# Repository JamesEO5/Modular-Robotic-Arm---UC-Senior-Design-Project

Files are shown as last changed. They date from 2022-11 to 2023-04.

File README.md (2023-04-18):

# Modular-Robotic-Arm---UC-Senior-Design-Project
This is a Modular Robot arm designed to be simple to build and modify. The target audience is grade school and high school students interested in STEM. All files needed to build this robot can be accessed in this database. An instruction manual is also added so that anyone interested in constructing this robot is able to in the easiest way possible. 

To navigate this site click on the desired folder to view each file and download them. 
The instruction manual should be your first resource since it contains links to all of the stp files needed for the build as well as links to all of the purchaseable parts needed. 

This github page was created by James O'Meara with the help from Charles Watson and Roger Farnham.

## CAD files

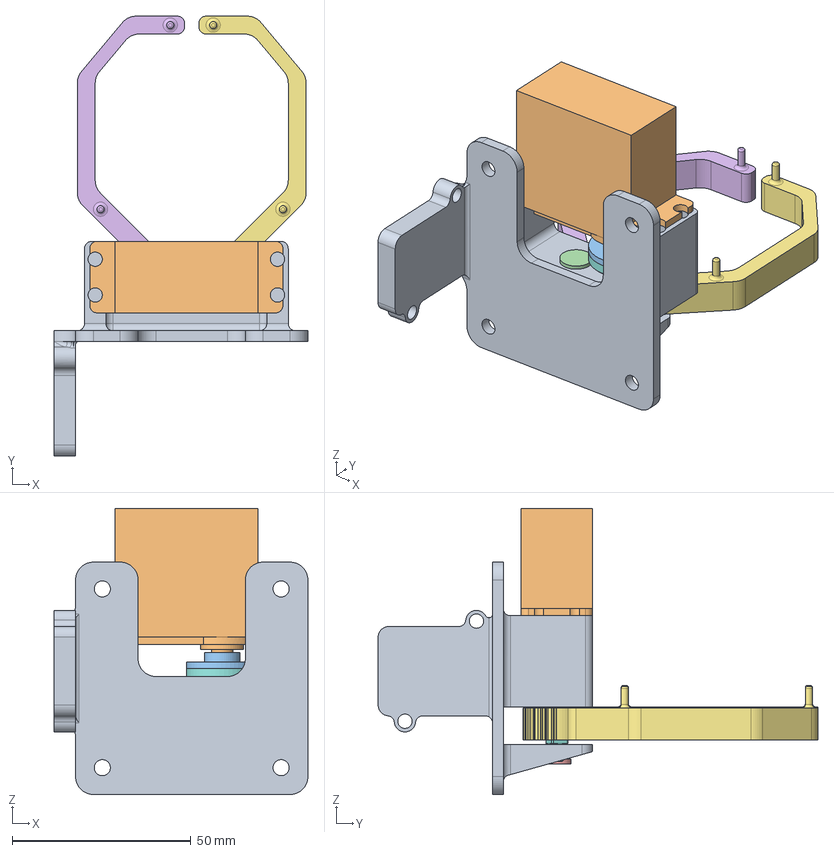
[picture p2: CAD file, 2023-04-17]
3D Files/Claw/ClawAssembly.stp
71.0 x 123.0 x 80.0 mm
ClawBody
MG996R_10KGSERVO
FlangeHorn
claw shaft
ClawShaftSpacer
Gripper_Left
Gripper_Right
Driveshaft_Claw

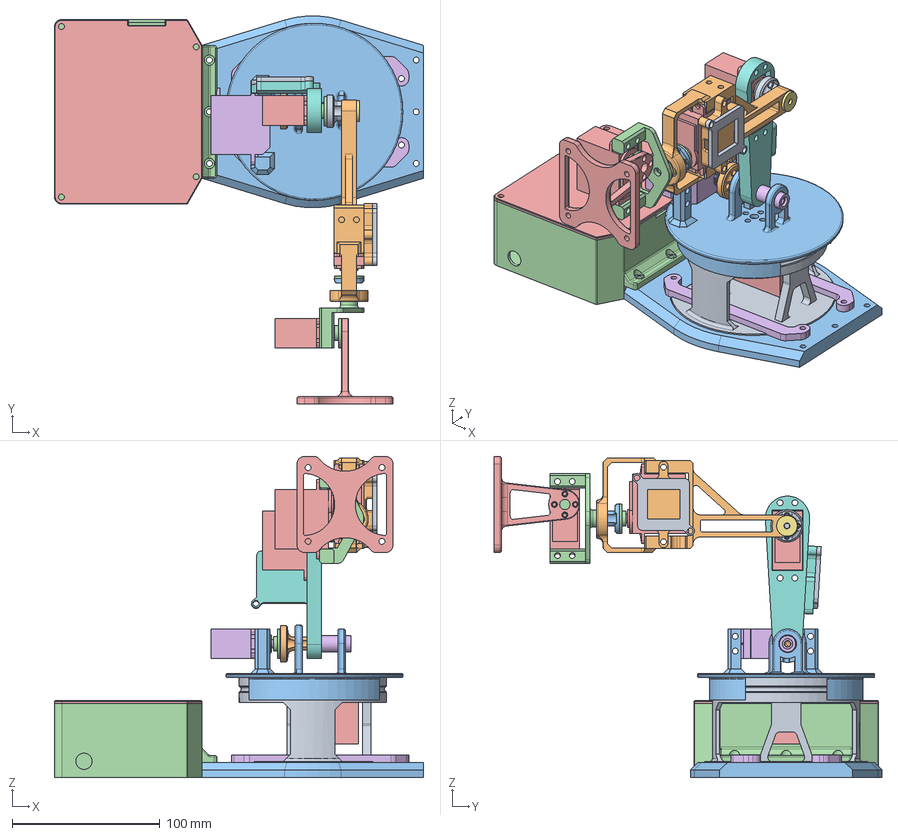
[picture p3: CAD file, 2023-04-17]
3D Files/Arm/MainAssembly.stp
250.0 x 262.8 x 217.4 mm
Base
DriveshaftLower
Turntable
FlangeHorn x 5
MG996R_10KGSERVO x 4
DS3225MG_25KGSERVO
10x15bearing x 2
Link1
DriveshaftUpper
Link2
BearingShaftA
BearingPlate
EEPlate
SupportBushing
UpperLinkWasher
JB_Link1
JB_Lid x 2
JB_Link2
BP_Center
BP_EBox
BP_EBox_Lid
HoldingBar x 2

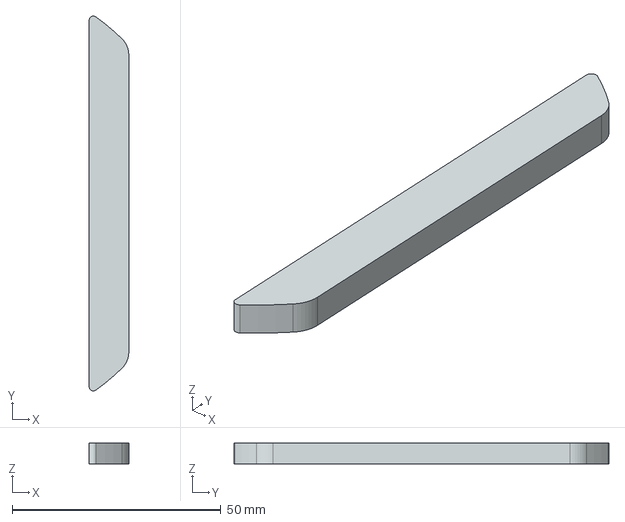
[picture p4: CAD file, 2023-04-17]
3D Files/Arm/BP_Spacer.stp
9.50 x 89.7 x 5.00 mm

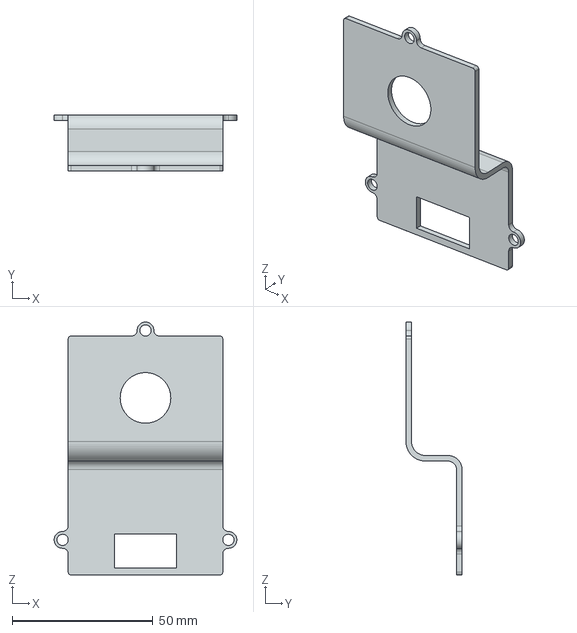
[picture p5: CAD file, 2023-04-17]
3D Files/Camera Holder/CM_Lid.stp
65.0 x 20.0 x 90.0 mm

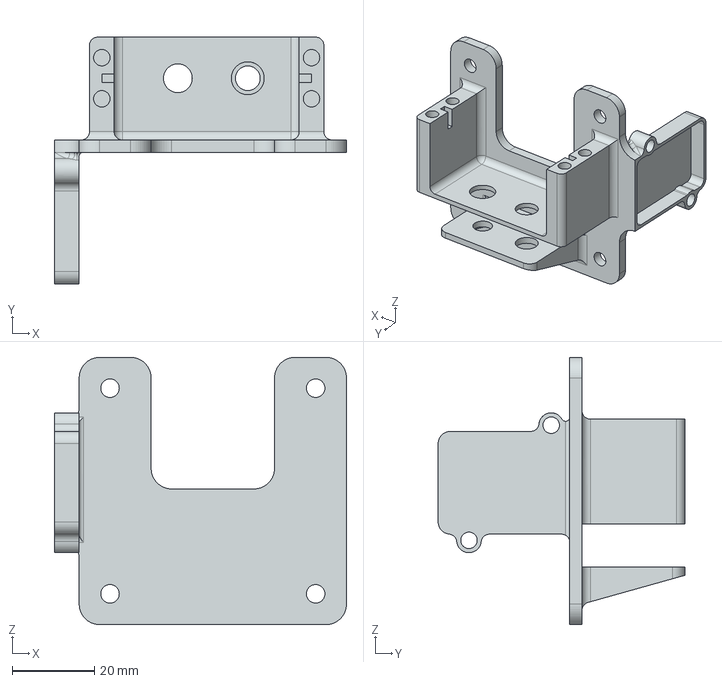
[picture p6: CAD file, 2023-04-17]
3D Files/Claw/ClawBody.stp
71.0 x 60.0 x 65.0 mm

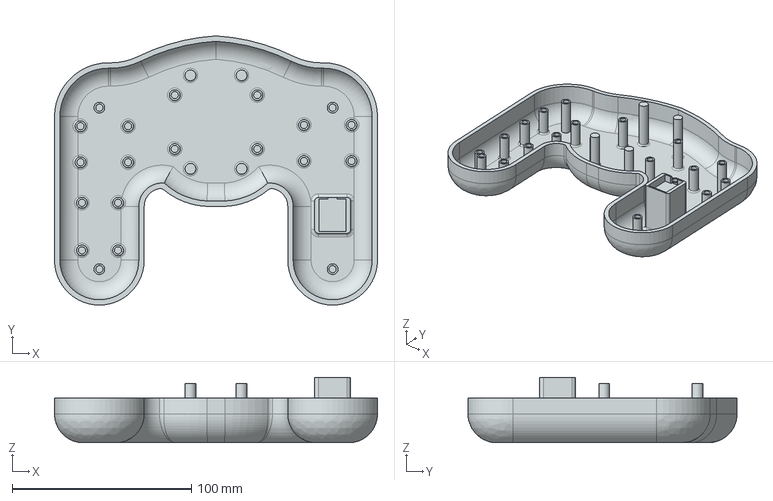
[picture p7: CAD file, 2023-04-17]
3D Files/Controller/Controller Bottom v2.stp
180.0 x 150.0 x 36.5 mm

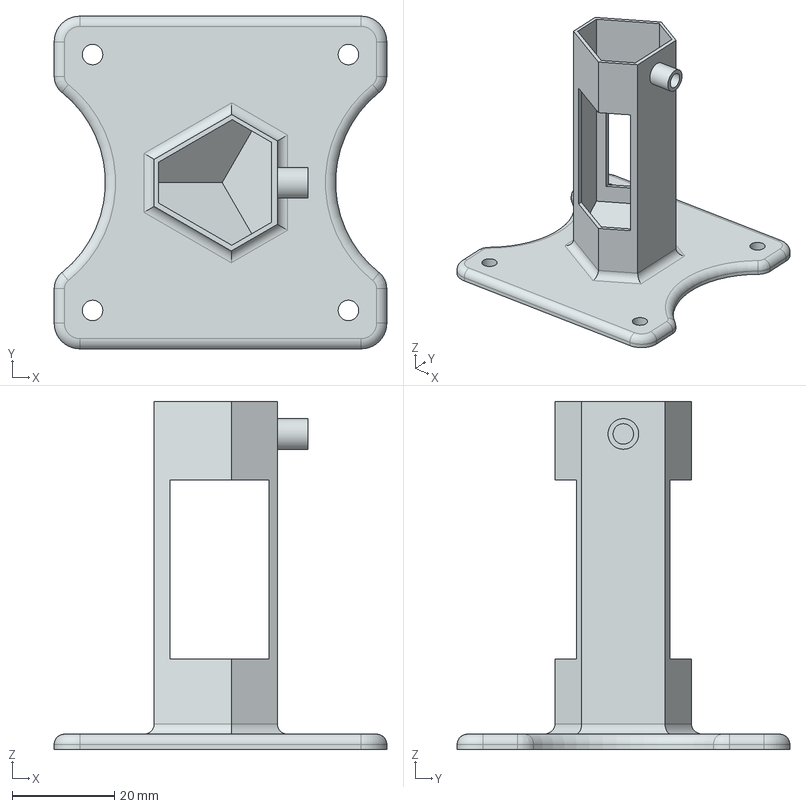
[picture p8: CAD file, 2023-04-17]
3D Files/Pen Holder/Pen end effector V6.stp
65.0 x 65.0 x 68.0 mm

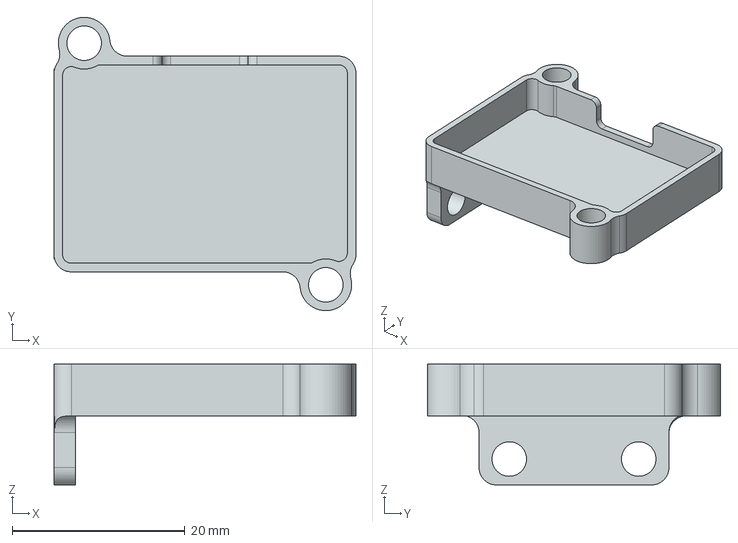
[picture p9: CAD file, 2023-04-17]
3D Files/Arm/JB_EEPlate.stp
35.0 x 34.0 x 14.0 mm

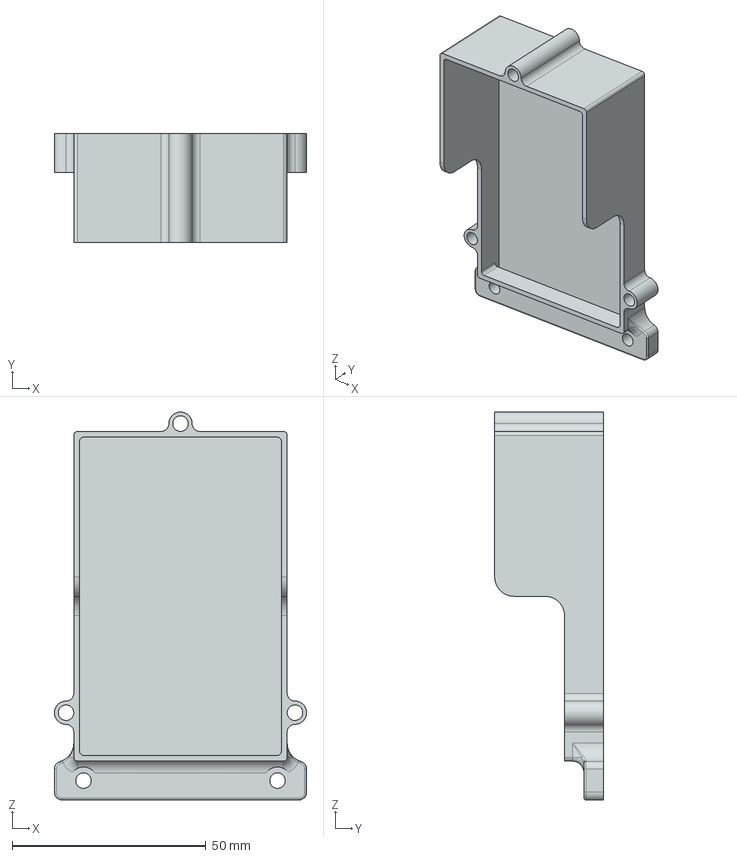
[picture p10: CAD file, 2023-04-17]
3D Files/Camera Holder/CM_Body.stp
65.0 x 28.0 x 100.0 mm

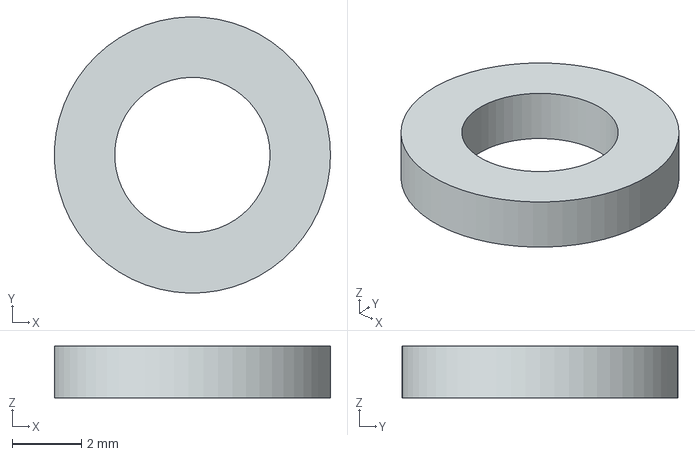
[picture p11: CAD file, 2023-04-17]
3D Files/Claw/ClawShaftSpacer.stp
7.99 x 8.00 x 1.50 mm

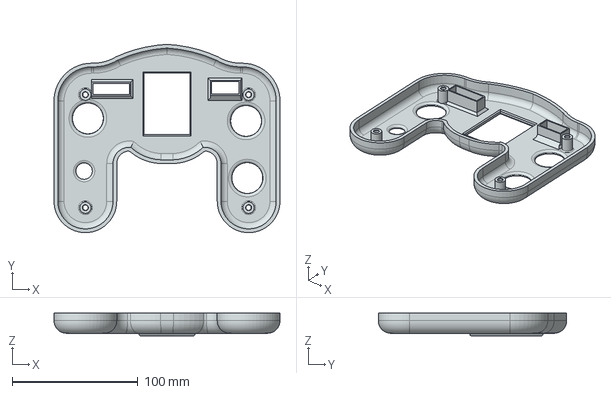
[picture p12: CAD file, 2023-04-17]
3D Files/Controller/Controller top v4.stp
180.0 x 150.0 x 18.0 mm

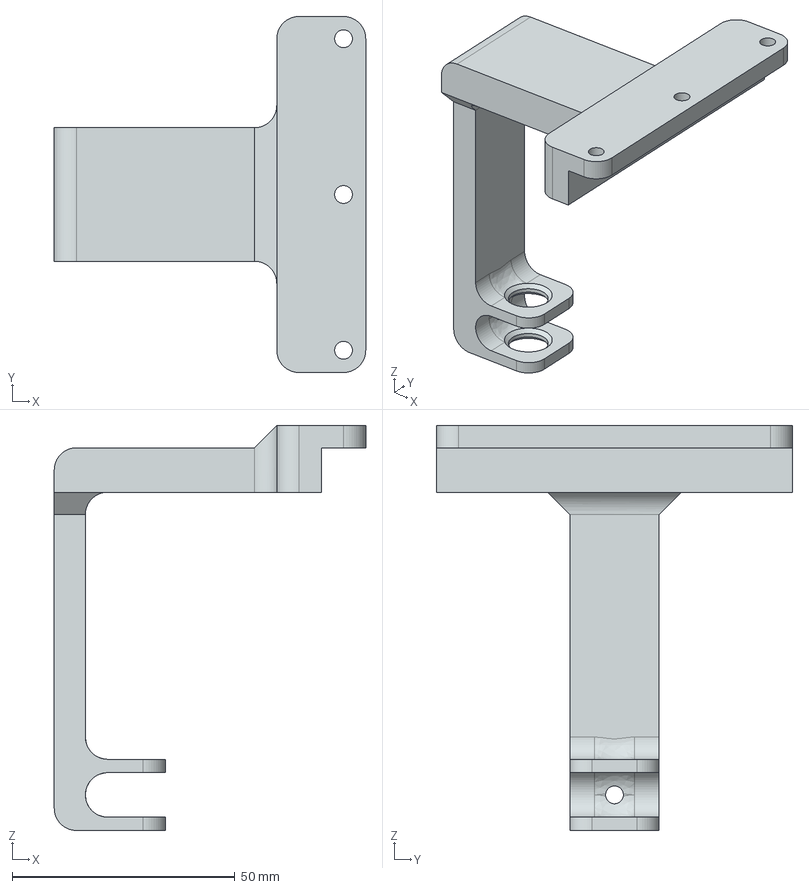
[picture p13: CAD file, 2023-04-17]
3D Files/Arm/BP_ClampPlate.stp
70.0 x 80.0 x 91.0 mm

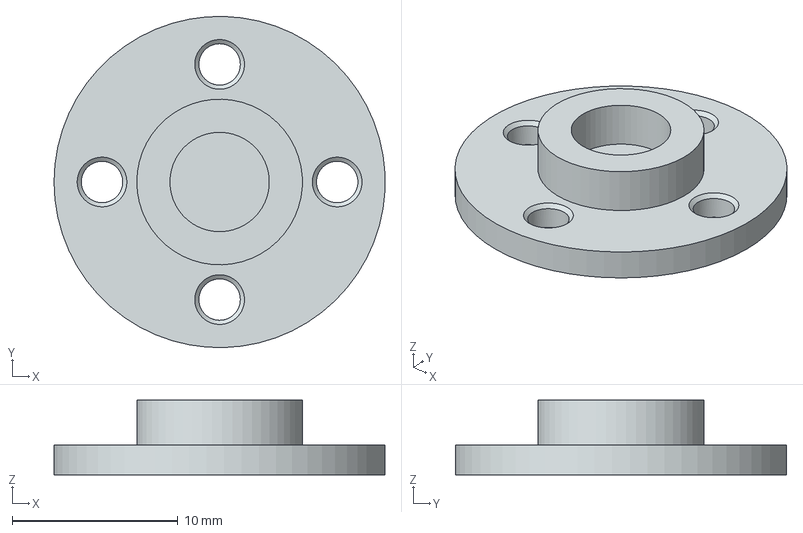
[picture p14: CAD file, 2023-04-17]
3D Files/Claw/FlangeHorn.stp
20.0 x 20.0 x 4.50 mm

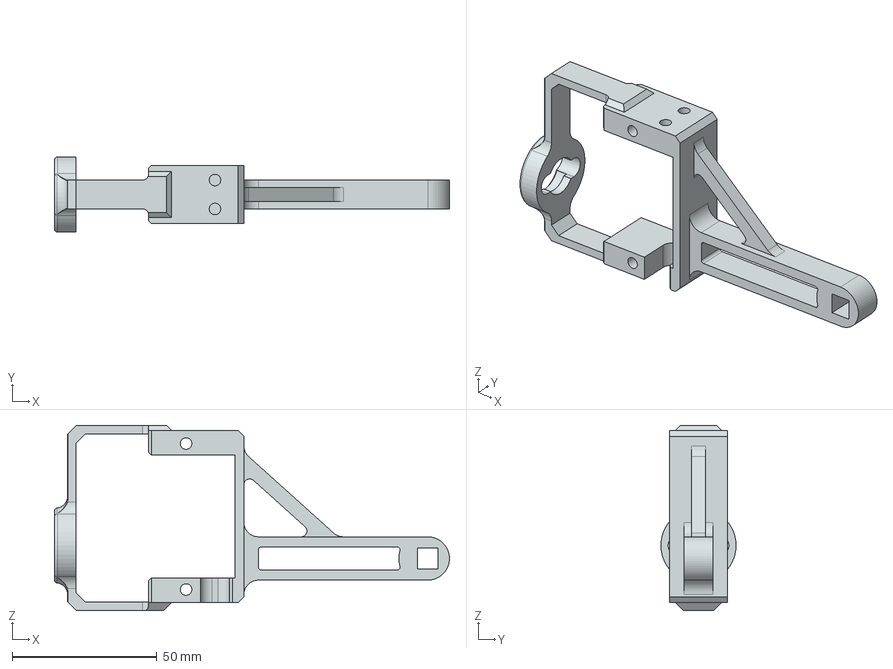
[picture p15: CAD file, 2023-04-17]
3D Files/Arm/Link2.stp
136.6 x 26.0 x 64.0 mm

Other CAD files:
3D Files/Arm/DriveshaftUpper.stp
3D Files/Claw/Gripper_Right.stp
3D Files/Arm/BearingPlate.stp
3D Files/Claw/claw shaft.stp
3D Files/Arm/10x15bearing.stp
3D Files/Arm/BP_Center.stp
3D Files/Arm/BP_ClampFoot.stp
3D Files/Arm/BP_ClampScrew.stp
3D Files/Arm/BP_ClampShaft.stp
3D Files/Arm/BP_EBox.stp
3D Files/Arm/BP_EBox_Lid.stp
3D Files/Arm/Base.stp
3D Files/Arm/BearingRetainer.stp
3D Files/Arm/BearingShaftA.stp
3D Files/Arm/ClawBody.stp
3D Files/Arm/DriveshaftLower.stp
3D Files/Arm/EEPlate.stp
3D Files/Arm/FlangeHorn.stp
3D Files/Arm/HoldingBar.stp
3D Files/Arm/JB_Lid.stp
3D Files/Arm/JB_Lid_EEPlate.stp
3D Files/Arm/JB_Link1.stp
3D Files/Arm/JB_Link2.stp
3D Files/Arm/Link1.stp
3D Files/Arm/SupportBushing.stp
3D Files/Arm/Turntable.stp
3D Files/Arm/UpperLinkWasher.stp
3D Files/Arm/servo.stp
3D Files/Claw/Driveshaft_Claw.stp
3D Files/Claw/Gripper_Left.stp

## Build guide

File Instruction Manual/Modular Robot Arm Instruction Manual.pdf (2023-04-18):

## USER MANUAL

# Modular Robotic Arm

### 3D Printed Modular Robot Arm

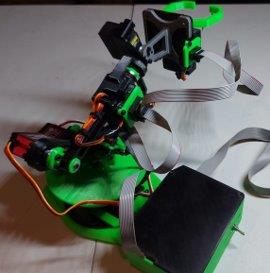
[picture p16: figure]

This document explains how to construct, use, and troubleshoot a 3D printed Modular Robot Arm. This robot arm uses a Arduino board to register inputs made by the user on a controller and use those inputs to control the servos on the arm. The modular design of this robot also encourages users to create their own features. All components of this arm are openly available online so that anyone can gather the materials themselves and build it. The open source code is also available so a user can modify to match their needs.

Note Read through the entire manual before assembling the robot. This will ensure no important information is missed before assembly.

# Contents

2 | Modular Robot Arm Manual

# Open Source Resources

All Files can be found on the git hub page.
- Git hub files are found at this link. (https://github.com/JamesEO5/Modular-Robotic-Arm---UC-Senior-Design-Project)
- If this is not a pdf document then they can be found at:
- https://github.com/JamesEO5/Modular-Robotic-Arm---UC-Senior-Design-Project

# Tools Required

1. #25 Allen Key
2. #25 Phillips Head Screwdriver
3. Soldering Iron
4. Pliers jjbjbjb

jij

# Safety Guidelines

Caution Observe all instructions and cautions in the user documentation. Constructing the robot
arm in a manner not specified can damage the robot arm and injure the user.

Caution The protection provided by the model can be impaired if it is used in a manner not described in the user documentation.

Caution Electrical shock hazard. This device contains electrical components and capacitors. Do
not disassemble the electronics ofhe robot while it is in operation and be sure to discharge the capacitors before disassembly.

Caution Risk of fire if electrical shorts occur. Some 3D printed plastics can burn and catch on fire.

# EMC Notices

Refer to the following notices for prevention measures necessary to ensure the specified EMC performance.

Notice For EMC declarations and certifications, and additional information, refer to the Product Certifications and Declarations section.

Notice The performance of this product can be disrupted if subjected to Electrostatic Discharge (ESD) during operation. To prevent damage, industry- standard ESD prevention measures must be employed during installation, maintenance, and operation.

# Purchasable Parts

## Mechanical Components

1. #25 Screws
2. Servo Horns
3. M3 x 5mm Female Press In Inserts

## Cables

1. 8 Pin Ribbon Connectors
2. 20 Pin Ribbon Connectors
3. 8 Pin Ribbon Cable
4. 20 Pin Ribbon Cable

## Electrical Components

1. Power Adapter
2. Power Supply
3. 25kg Servo
4. 10kg Servo

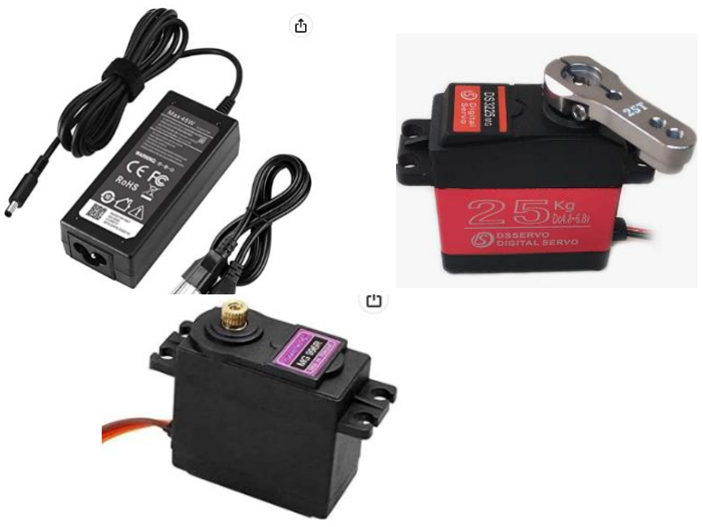
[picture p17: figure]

# 3D Printed Parts

## Base

1. Base
2. BP_Center
3. BP_EBox
4. BP_EBox_Lid
5. HoldingBar
6. Turntable
7. ClampFoot
8. ClampSHaft
9. ClampPlate
10.BearingShaftA
11.DriveshaftLower

## Link 1

1. Link1
2. JB_EEPlate
3. JB_Link1

## Link 2

1. Link 2
2. BearingPlate
3. JB_Lid_EEPlate
4. EEPlate
5. JB_Lid
6. JB_Link2
7. DriveshaftUpper
8. UpperLinkWasher

## Gripper

1. ClawBody
2. Gripper_Right
3. Gripper_Left
4. Driveshaft_Claw
5. Claw_Shaft
6. ClawShaftSpacer

## Controller

1. Controller_Top
2. Controller_Bottom

# Before Assembly

Complete the following tasks before building the Modular Robot Arm. It is very important that you complete the tasks before building to ensure easy assembly and best performance.
1. Purchase all necessary parts.
2. Print all parts that need to be 3D printed.
3. Be sure your work surface is completely free of other materials not related to the build.

# Wiring Instructions

## Controller

1 | Start by soldering the 8 and 20 pin connector to the controller motherboard. Then solder the straight 8 pin connector to the bottom section of the controller board
2 | Flip the board over and solder 5 wires to the underside of the board according to the picture seen Then connect the J3 joystick to the wires as seen
3 | Turn the board back over to the top side and solder 5 wires to the top of the board Then solder those wires to the J1 joystick as seen

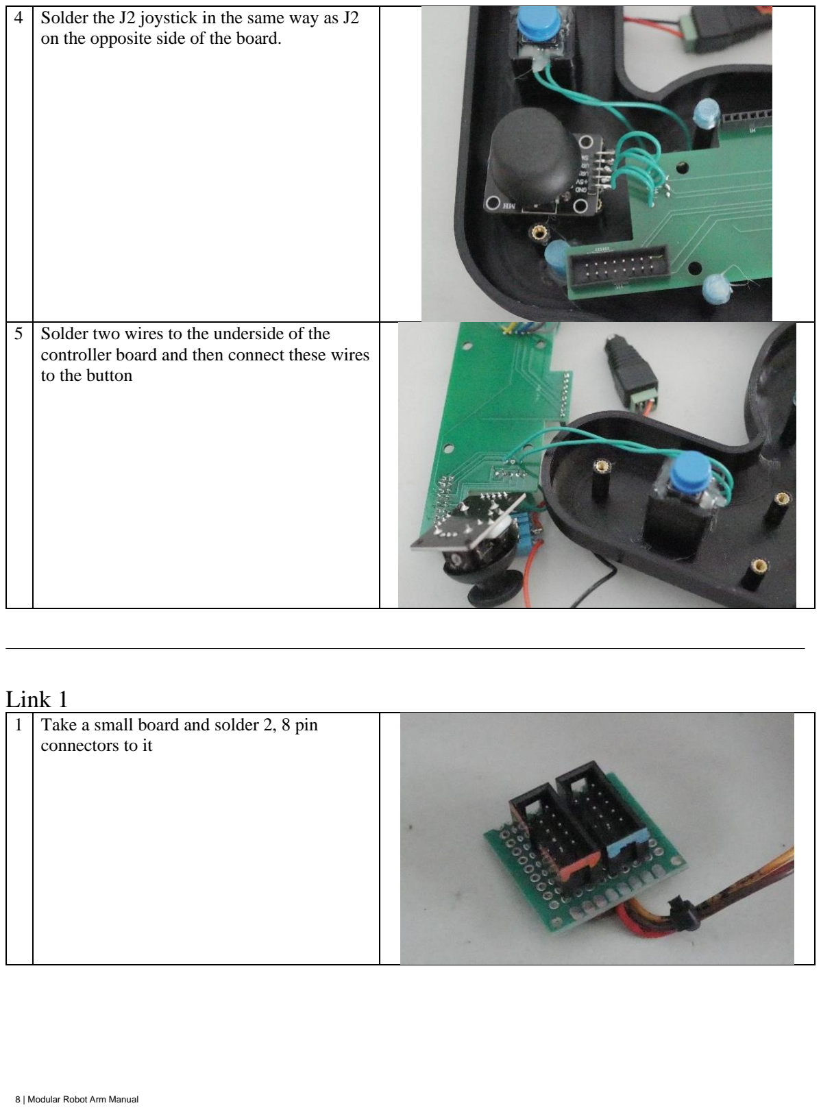
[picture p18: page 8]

4 | Solder the J2 joystick in the same way as J2 on the opposite side of the board.
5 | Solder two wires to the underside of the controller board and then connect these wires to the button

## Link 1

1 Take a small board and solder 2, 8 pin connectors to it

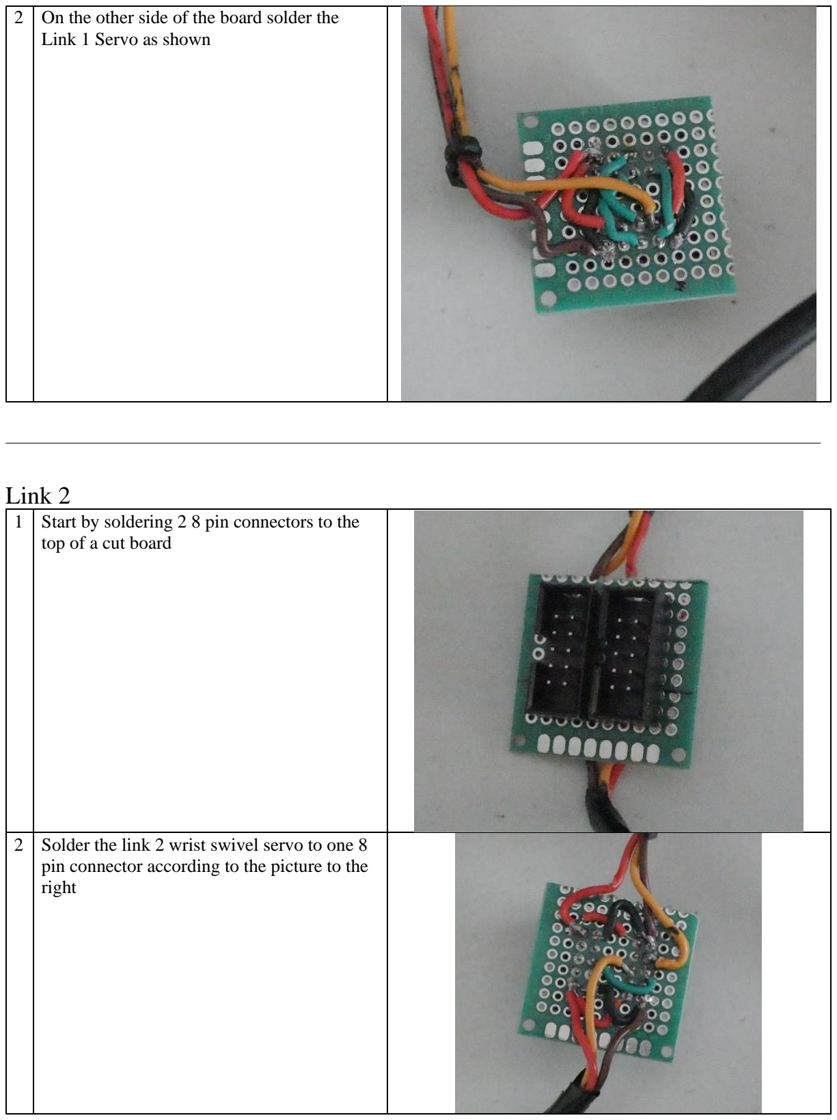
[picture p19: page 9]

2 On the other side of the board solder the Link 1 Servo as shown

## Link 2

1 | Start by soldering 2 8 pin connectors to the top of a cut board
2 | Solder the link 2 wrist swivel servo to one 8 pin connector according to the picture to the right

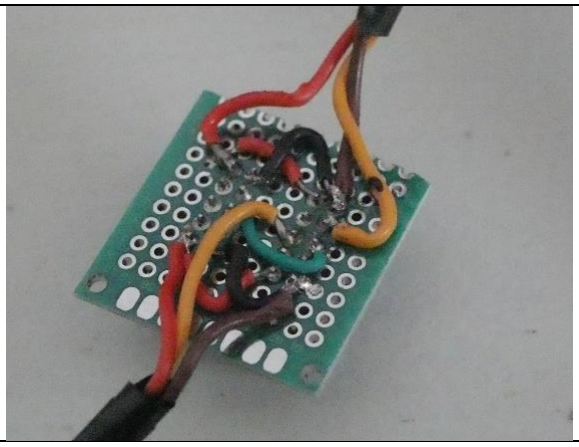
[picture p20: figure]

3 Solder the link 2 wrist bend servo to the other 8 pin connector according to the picture to the right

## Gripper

1 | Solder the 8 pin connector to a small board
2 | Solder the gripper servo to the board as seen on the right

## Main Board

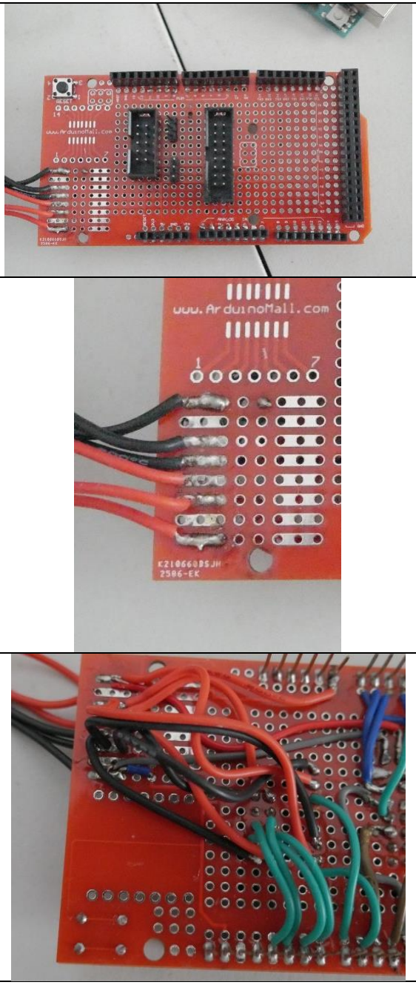
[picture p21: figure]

1 | Solder an 8 pin connector, a 20 pin connector, and 2 3 pin connectors to a Arduino cover board as shown
2 | Solder 3 black wires and 3 red wires to the side of the board as shown
3 | Flip the board over and solder red and black wires to the board as shown to the right

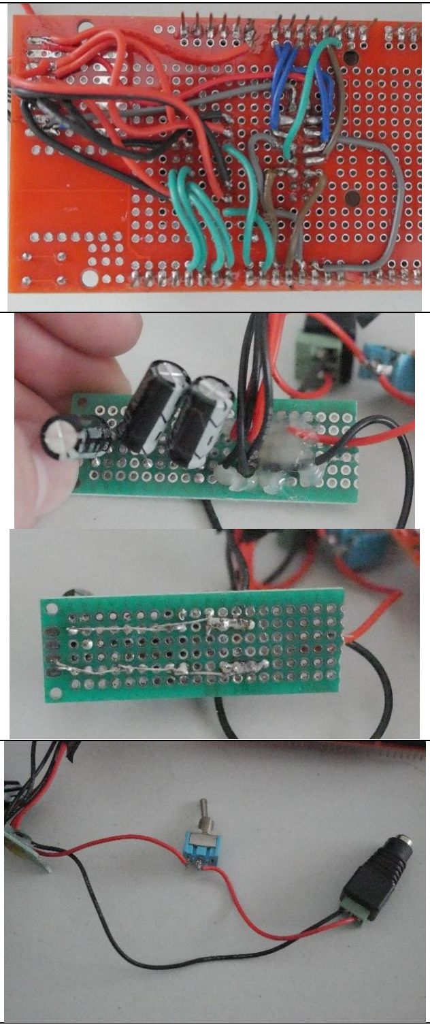
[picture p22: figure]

4 | Solder the rest of the blue and green wires to the board as shown to the right. These wires are for the pin outs for the servos and controller
5 | Take another small board and solder the red and black wires coming off the board in parallel with their respective colors. Then solder 3 capacitors in parallel with the red and black wires
6 | Finally solder a power input in series with the red and black wires and add a switch to the red wire. Wire it according to the picture to the right

# Build Instructions

When building the robot arm use the #25 screw driver on all Phillips head screws and a #25 allen wrench on all other fasteners. Follow the instructions carefully and follow each step to ensure no components are damaged during the build process. Be sure to also follow all wiring guides mentioned so no wires get entangled during operation.

## Gripper

1 | Parts Required: 1. 10 short screws 2. 2 medium screws 3. 1 servo bracket screw 4. gripper pin 5. Washer 6. Aluminum servo interface bracket 7. Gripper interface pin 8. Servo circuit board cover 9. Left and right grippers 10. 10 kg Servo 11. Servo Bracket 12. Hand Connector bracket
2 | Place the Hand connector bracket on the large flat surface of the servo bracket and secure it with 4 short screws
3 | Snap on the aluminum servo interface bracket onto the 10kg servo and secure it with the servo screw

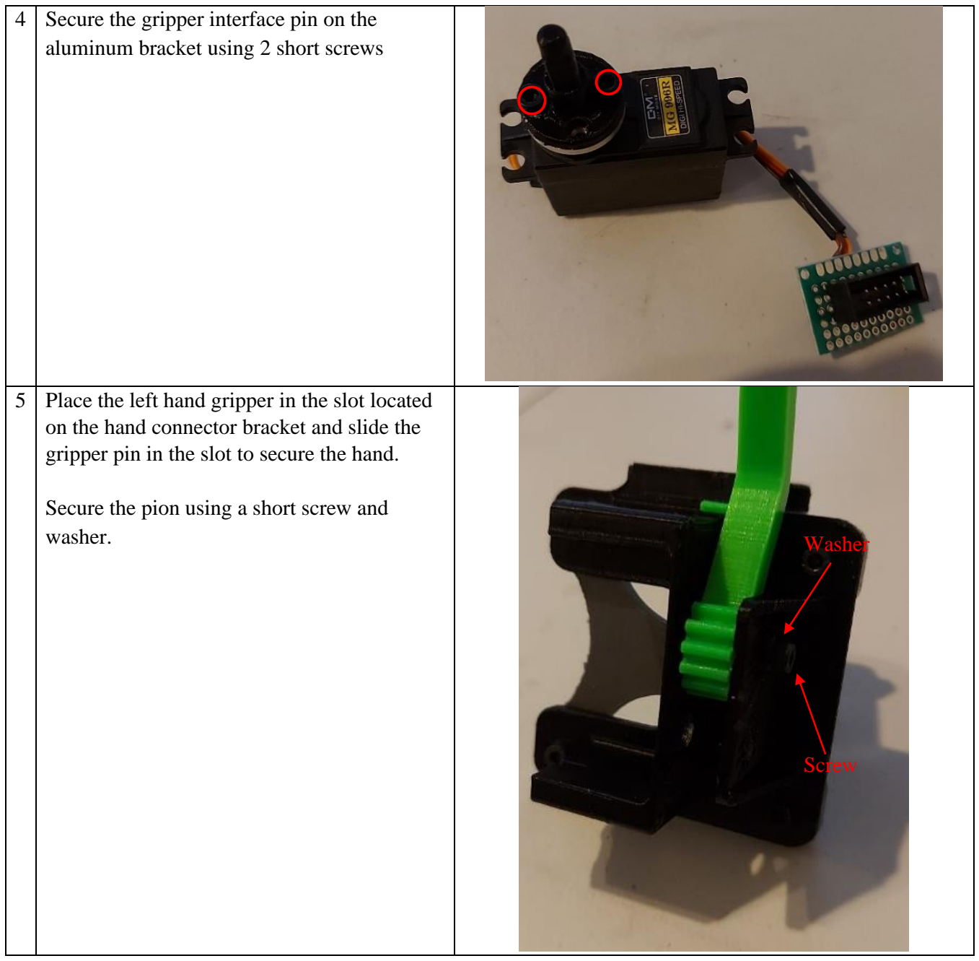
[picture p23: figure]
aluminum bracket using 2 short screws; Secure the pion using a short screw and; washer.; Washer; Screw

4 | Secure the gripper interface pin on the
5 | Place the left hand gripper in the slot located on the hand connector bracket and slide the gripper pin in the slot to secure the hand.

6 | Place the right hand gripper in the other slot and interface the gears with the left gripper Secure the right gripper with the servo assembly and fasten 2 medium screws through the servo holes and into the servo bracket
7 | Place the circuit board connected to the servo in the circuit board slot on the servo bracket
8 | Secure the circuit board using the circuit board cover and fasten it down using 2 short screws

## Link 2

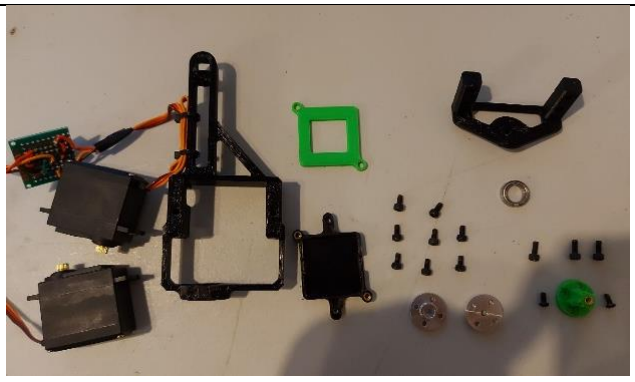
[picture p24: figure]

1 | Parts Required: 1. 2 10kg Servos connected with circuit board 2. Wrist/Elbow bracket 3. Circuit board mount 4. Circuit board cover 5. hand Servo Bracket 6. Bearing 7. 8 short screws 8. 2 aluminum servo interface bracket 9. 3 medium screws 10. 2 servo screws 11. wrist interface pin
2 | Place one of the aluminum servo interface brackets on the wrist servo and secure it with a servo screw

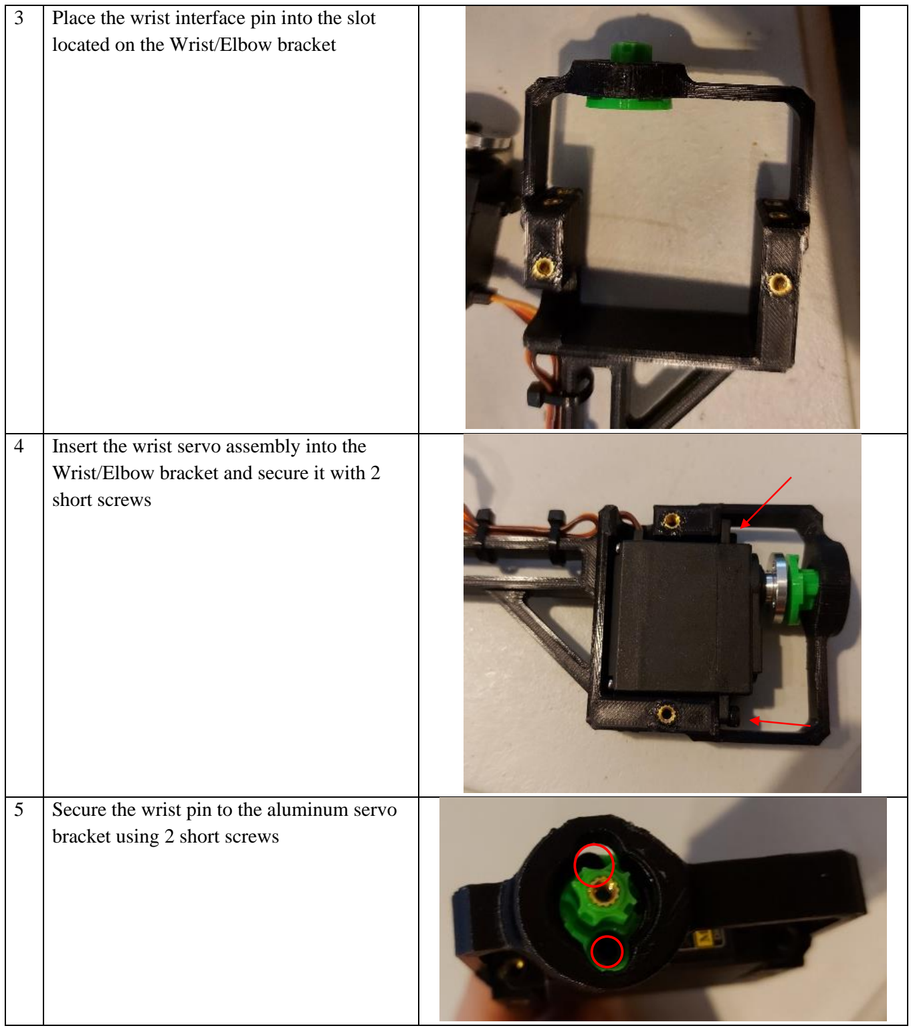
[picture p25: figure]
located on the Wrist/Elbow bracket

3 | Place the wrist interface pin into the slot
4 | Insert the wrist servo assembly into the Wrist/Elbow bracket and secure it with 2 short screws
5 | Secure the wrist pin to the aluminum servo bracket using 2 short screws

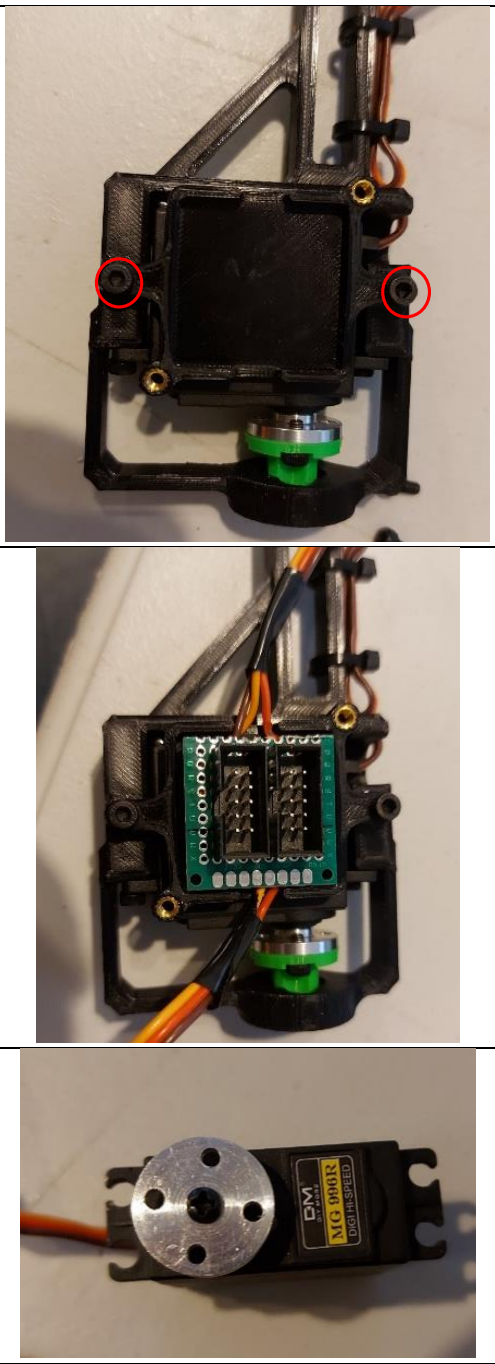
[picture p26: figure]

6 | Place the circuit board mount onto the Wrist/Elbow bracket and secure it with 2 short screws
7 | Place the circuit board for the servos into the circuit board mount
8 | Place the other aluminum servo bracket onto the servo and secure it with a servo screw

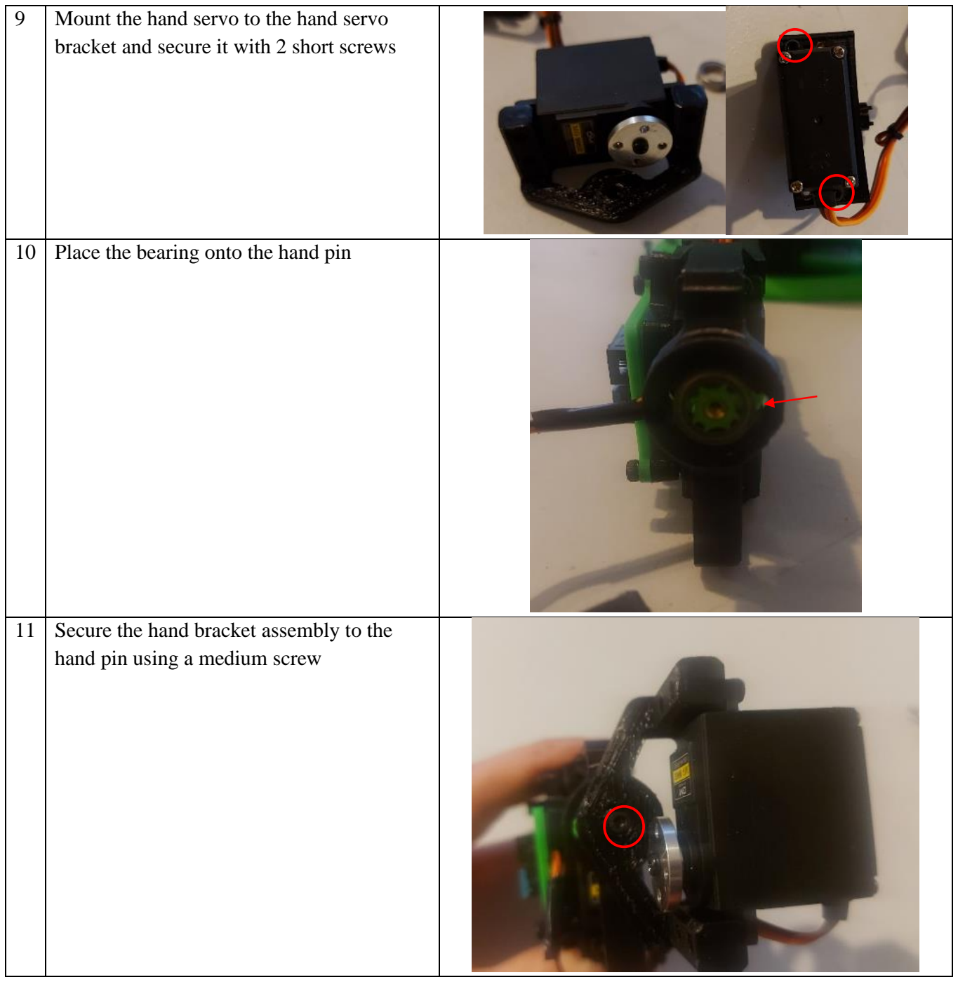
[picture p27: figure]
Place the bearing onto the hand pin

9 | Mount the hand servo to the hand servo bracket and secure it with 2 short screws
11 | Secure the hand bracket assembly to the hand pin using a medium screw

## Link 1

1 | Parts list 1. 25kg servo 2. Circuit board mount 3. 6 medium screws 4. 4 short screws 5. Aluminum servo interface bracket 6. Elbow pin 7. Servo screw 8. Circuit board cover 9. Elbow/Shoulder
2 | Secure the circuit board mount to the elbow/shoulder bracket using 2 medium screws
3 | Snap on the aluminum servo bracket and secure it with the servo screw

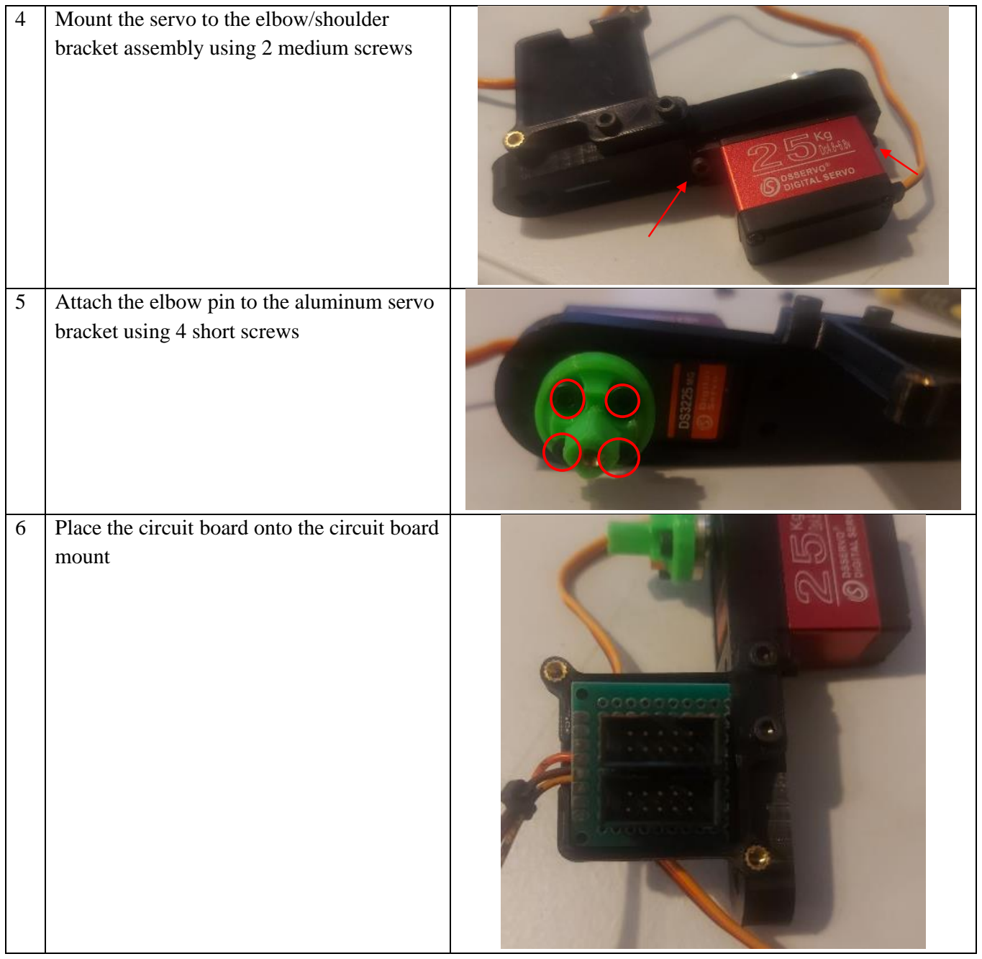
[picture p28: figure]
mount

4 | Mount the servo to the elbow/shoulder bracket assembly using 2 medium screws
5 | Attach the elbow pin to the aluminum servo bracket using 4 short screws
6 | Place the circuit board onto the circuit board

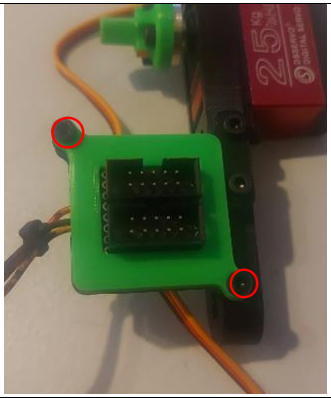
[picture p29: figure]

7 Attach the circuit board cover to the circuit board mount using 2 medium screws

## EEBox

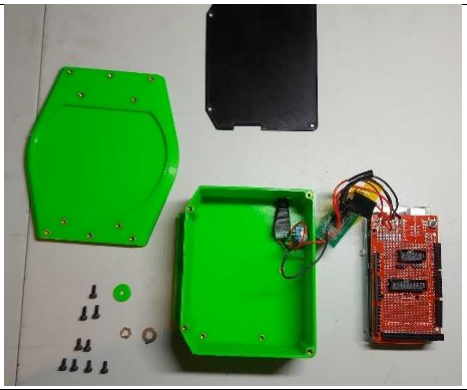
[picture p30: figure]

1 Parts list

1. Main Circuit board
2. Main Board box
3. Main board box cover
4. Arm base
5. 3 long screws
6. 6 medium screws
7. Switch washer
8. Switch nut
9. Wide washer

2 | Hot glue the switch and power plug to the bottom of the main board box
3 | Secure the switch using the switch washer and nut
4 | Place the main board and auxiliary board in the main board box and secure them with 3 medium screws and the large washer
| The auxiliary board is secured using one of the screws and washer
| The main board is secured using 2 of the screws

Nut

Washe

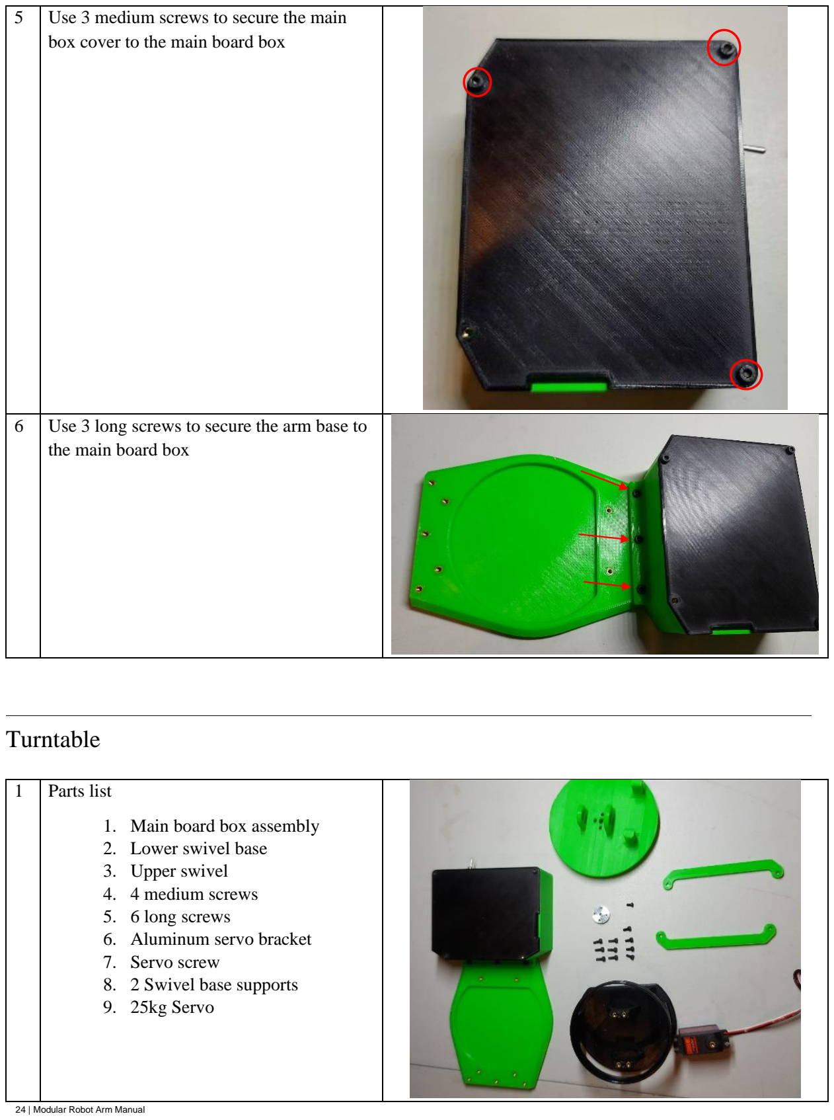
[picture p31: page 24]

5 | Use 3 medium screws to secure the main box cover to the main board box
6 | Use 3 long screws to secure the arm base to the main board box

## Turntable

1 Parts list

1. Main board box assembly
2. Lower swivel base
3. Upper swivel
4. 4 medium screws
5. 6 long screws
6. Aluminum servo bracket
7. Servo screw
8. 2 Swivel base supports
9. 25kg Servo

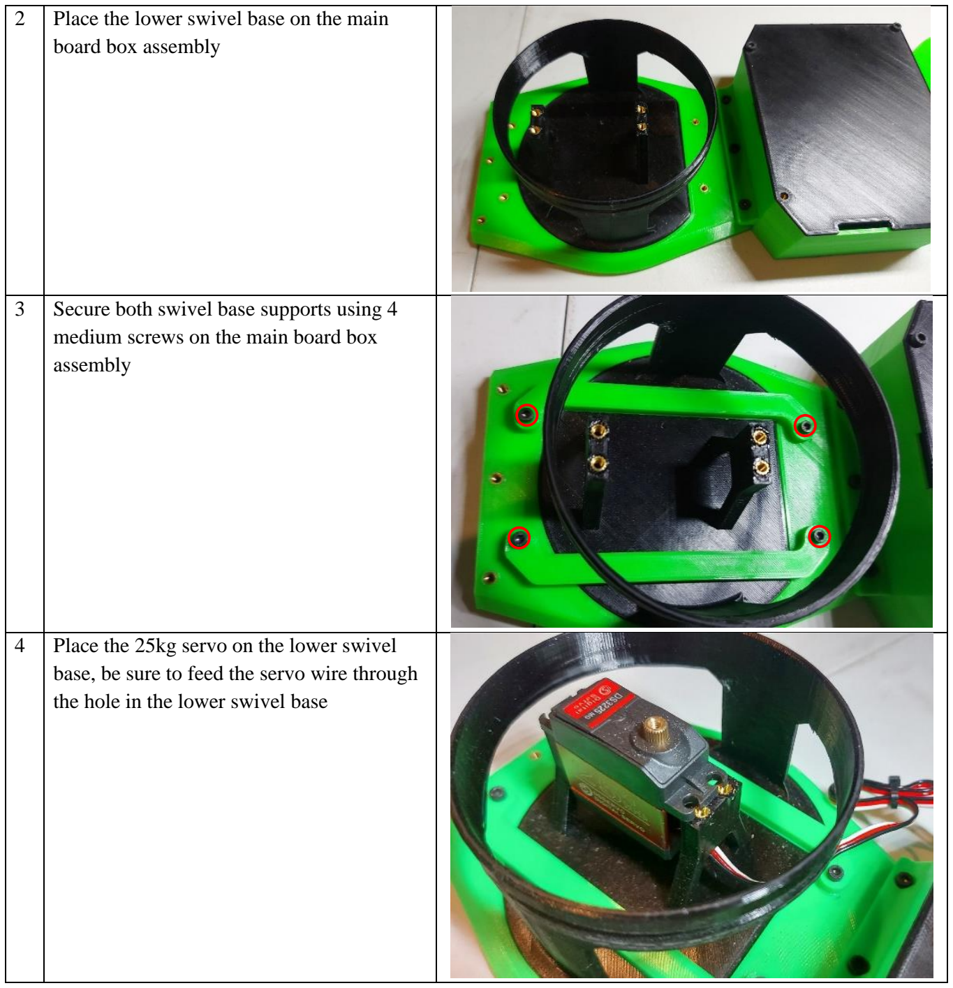
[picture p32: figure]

2 | Place the lower swivel base on the main board box assembly
3 | Secure both swivel base supports using 4 medium screws on the main board box assembly
4 | Place the 25kg servo on the lower swivel base, be sure to feed the servo wire through the hole in the lower swivel base

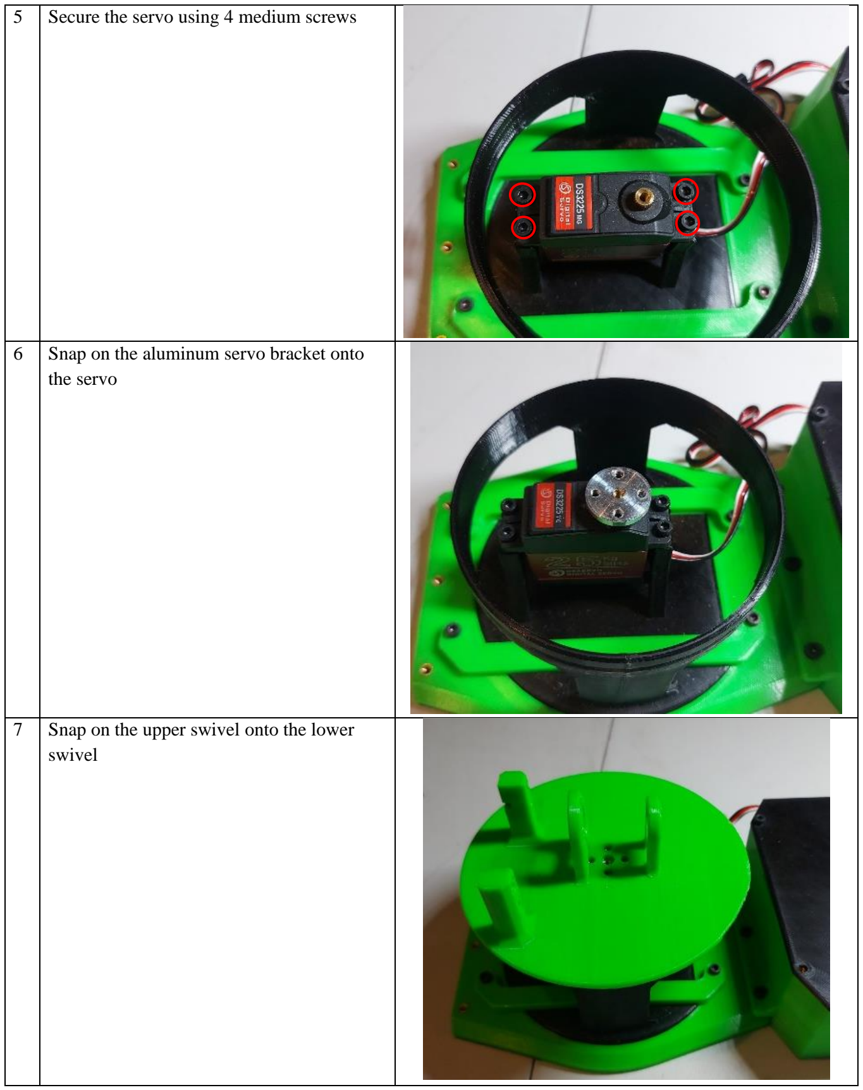
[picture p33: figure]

5 | Secure the servo using 4 medium screws
6 | Snap on the aluminum servo bracket onto the servo
7 | Snap on the upper swivel onto the lower swivel

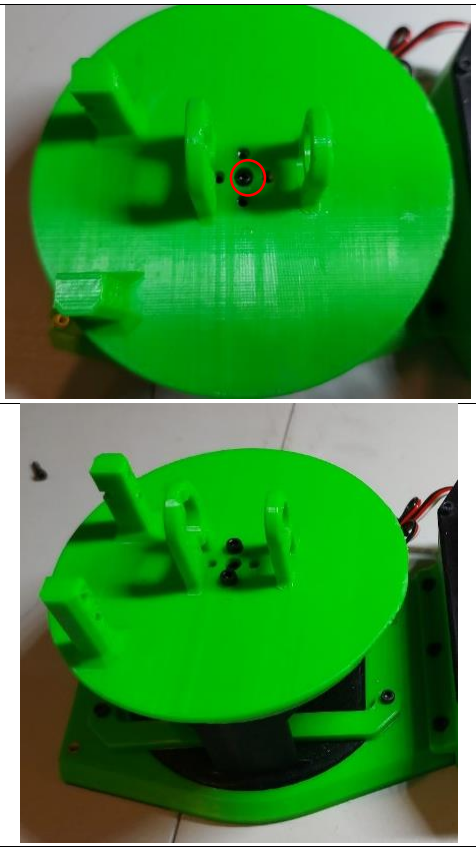
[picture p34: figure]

8 | Secure the upper swivel to the 25kg servo using the servo screw
9 | Secure the upper swivel base to the aluminum servo bracket using 2 medium screws

## Shoulder Joint

1 Parts list

1. 25kg servo
2. 4 long screws
3. 2 medium screws
4. Aluminum servo bracket
5. Bearing
6. Servo screw
7. Shoulder pin
2 | Snap the aluminum servo bracket onto the 25kg servo and secure it with the servo screw
3 | Attach the shoulder pin to the servo and secure it with 4 medium screws

4 | Place the bearing onto the shoulder pin
5 | Place the shoulder servo assembly on the upper swivel base Be sure to place the bearing into the upper swivel bearing brace
6 | Secure shoulder servo to the upper swivel using the 2 short screws

# Final Assembly

During final assembly the robot will need to be turned on before attaching all of the finished joints together. To prevent electrical shock or damage to your components be sure all wires are free from entanglement prior to turning the robot on. Also make sure the electrical box is closed so the power cables inside are not accidentally touched.

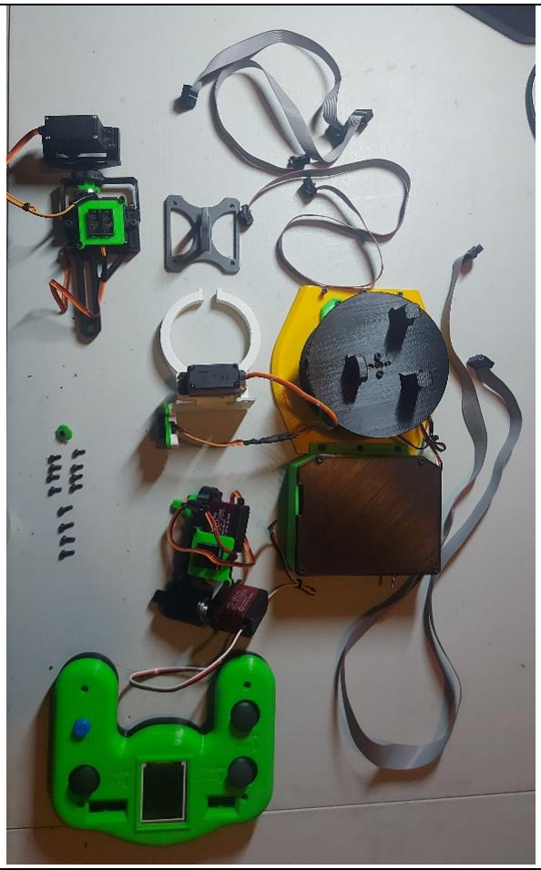
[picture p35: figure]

1 Parts List:
1. Base
2. Link 1
3. Link 2
4. Connector Bracket
5. Gripper
6. 3, 8 pin Cables
7. 1, 20 pin Cable
8. Controller
9. 12 screws
10. 1 screw with washer

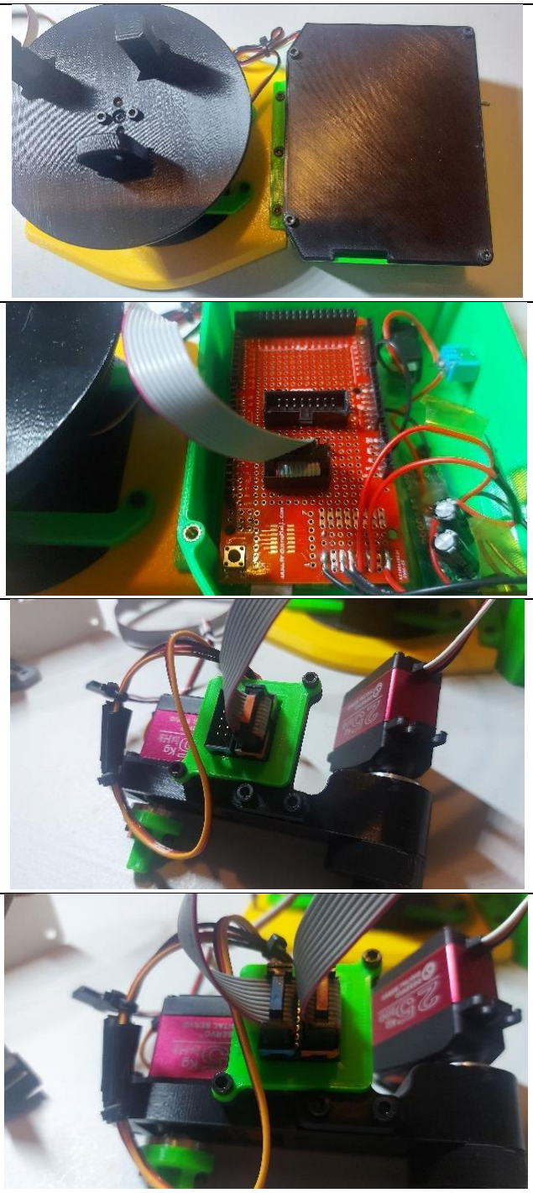
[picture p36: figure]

2 | Remove the BP_EBox_Lid from the BP_EBox
3 | Connect a 8 rib cable to the 8 rib connector
4 | Connect the other end of the 8 rib cable to the lower connector on Link 1
5 | Connect another 8 rib cable to the upper connector on link 1

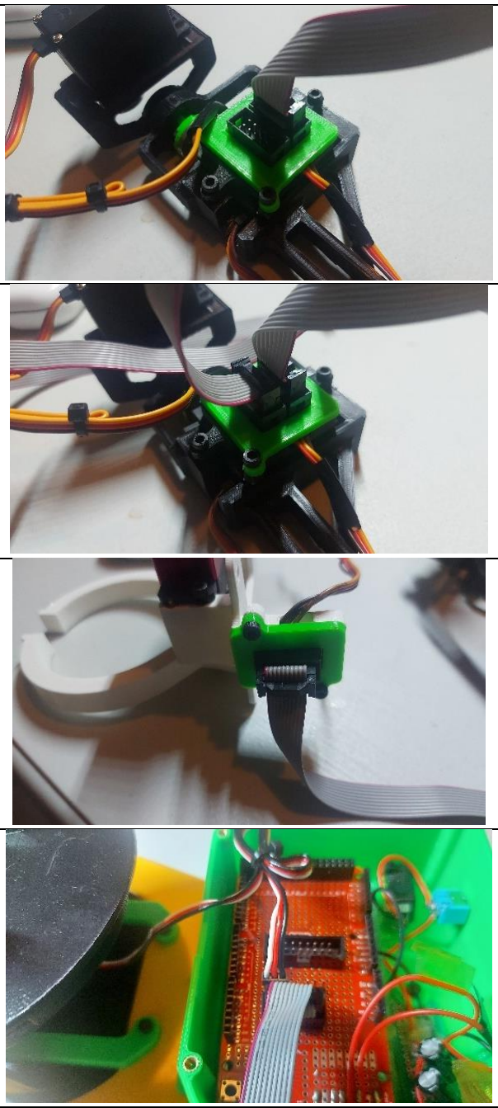
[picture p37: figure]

6 | Connect the other end of this 8 rib cable to the lower connector of link 2
7 | Connect another 8 rib connector to the upper connector of link 2
8 | Connect the other end of this 8 rib cable to the connector on the Gripper
9 | Connect the turntable servo connector to the 3 pins closest to the turntable

10 | Connect the shoulder servo connector to the 3 pins furthest from the turntable
11 | Connect the 20 rib connector to the Arduino board and then the controller
12 | Be sure the switch on the side of the BP_EBox is switched to the off position
13 | Plug in the power supply to the BP_EBox and plug the power supply into the wall

14 | Make sure all cables and parts are free to move before switching the switch to the on position
15 | Move the switch to the on position
16 | Now the final assembly of the robot can begin When the robot is first switched on all of the servos will move to their middle position and this will make sure that during assembly the connected positions will be correct

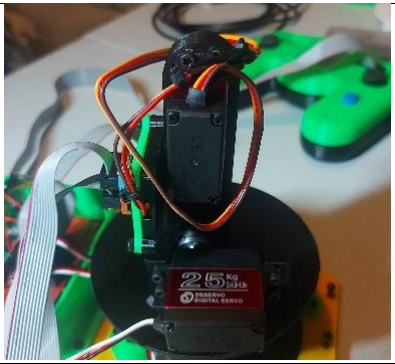
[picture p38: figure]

17 | Attach link 1 to the base Make sure link 1 is pointing straight up Connect Link 1 by first sliding the shaft into the turntable hole and then securing the servo to the mounts using 4 screws.

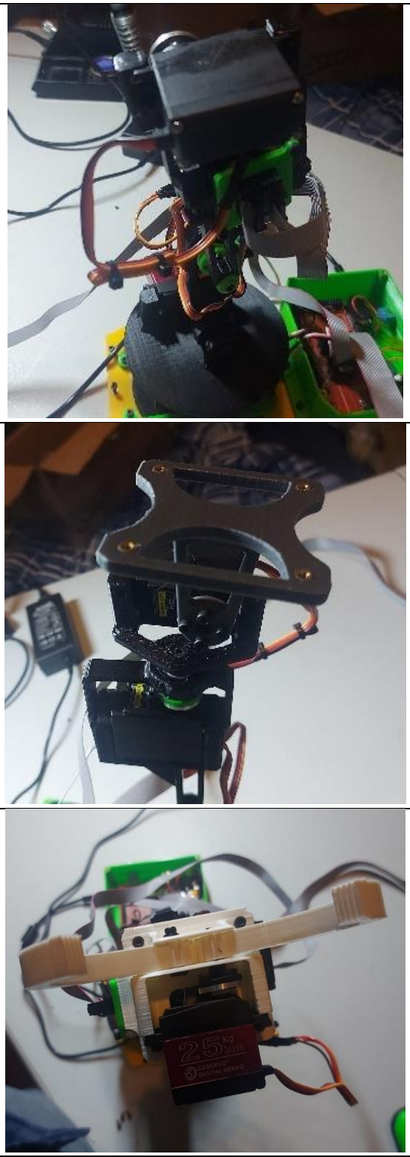
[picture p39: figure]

18 | Attach link 2 to link 1 Make sure link 2 is pointing straight up
| Attach link 2 by sliding the lower portion onto the axle and then securing it with the washer and screw
19 | Attach the connector bracket to Link 1 using 4 screws Be sure it is pointing straight up
20 | Attach the gripper to link 1 Be sure the gripper is pointing straight up Attach it to the connector bracket using 4 screws
21 | The robot is now fully functional and can be controlled using the controller

# Using the Robot

After you have finished building the robot it is ready to be operated. You can use the controller to move the robot around and the gripper can be replaced with a marker that allow the user to write. There is also 2 main functions that the robot can do based on certain inputs you can find below

## Controller:

- Joysticks
- J1
- Up and down controls the Shoulder joint
- Left and Right controls the turntable
- Pushing down the joystick performs the wave
- J2
- Up and Down controls the Elbow
- Left and right controls the wrist
- Pushing down the joy stick makes the robot draw UC
- J3
- Up and down controls the gripper swivel
- Left and right controls the gripper arms
- Other
- Home Button
- Returns the robot arm back to the home position
- Screen
- Once the camera is connected the screen shows the camera feed

# Troubleshooting Tips

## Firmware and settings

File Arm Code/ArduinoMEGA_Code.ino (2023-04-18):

//----------------------Initializing the Servo library, Servo Objects and Servo Pins------------------------------

#include <Servo.h>
Servo servo1; //base
Servo servo2; //link1
Servo servo3; //link1
Servo servo4; //link2
Servo servo5; //toolplate
Servo servo6; //gripper

#define s1pin 6 //Servo 1 to PWM enabled pin 6
#define s2pin 7 //Servo 2 to PWM enabled pin 7
#define s3pin 8 //Servo 3 to PWM enabled pin 8
#define s4pin 9 //Servo 4 to PWM enabled pin 9
#define s5pin 10 //Servo 5 to PWM enabled pin 10
#define s6pin 11 //Servo 6 to PWM enabled pin 11
//-------------------------Initializing Joystick X and Y Pins----------------------------------

//Joystick Pins333
#define J1x A0 //Controls Servo1
#define J1y A1 //Controls Servo2
#define J2x A2 //Controls Servo3
#define J2y A3 //Controls Servo4
#define J3x A4 //Controls Servo5
#define J3y A5 //Controls Servo6

//-----------------------Joystick Switches-------------------------
#define sJ1 2 //switch in J1 attached to interrupt pin 0
#define sJ2 3 //switch in J2 attached to interrupt pin 1
#define sJ3 4 //switch in J3 attached to interrupt pin 4
#define pB 5 //pushbutton

//--------------Declaration of Variables--------------------
//int zeroval = 1500; //1500 us --- neutral position
//int Jzeroval = 512; //home pos of joystick--deadband
int pos;

int pos1cons = 500;
int pos1final = 500;
int pos2cons = 0;
int pos2final = 0;
int pos3cons = 0;
int pos3final = 0;
int pos4cons = 0;
int pos4final = 0;
int pos5cons = 0;
int pos5final = 0;
int pos6cons = 0;
int pos6final = 0;

//------------------------- Switch Pins STATES------------------------------
int sJ1old;
int sJ2old;
int sJ3old;
int pBold;
int sJ1new;
int sJ2new;
int sJ3new;
int pBnew;

//---------------- millis Delay Variables------------------------------------
unsigned long
currTime, //current time
moveTime, //time when servo should move
speedofservo; //future code for varying speed

unsigned long timedelay = 5; //let time delay equal 15 milliseconds for now
unsigned long readtime = 5;

// Servo Range defined by min, and MAX, also initial position

int s1min = 500;
int s1ini = 1400;
int s1MAX = 2300;

int s2min = 1150;
int s2ini = 1675;
int s2MAX = 2200;

int s3min = 500;
int s3ini = 1400;
int s3MAX = 2300;

int s4min = 500;
int s4ini = 1500;
int s4MAX = 2500;

int s5min = 800;
int s5ini = 1550;
int s5MAX = 2300;

int s6min = 950;
int s6ini = 1375;
int s6MAX = 1800;

int pos1 = 512; //needs to be mapped to 1800
int pos2 = 512; //needs to be mapped to 1300
int pos3 = 512; //needs to be mapped to 1400
int pos4 = 512; //needs to be mapped to 1500
int pos5 = 512; //needs to be mapped to 1700
int pos6 = 512; //needs to be mapped to 1500

int v1;
int gripperspeed = 3; //changes the speed of gripper open and close

//**************************************     SET UP     ******************************************************

void setup() {
  //attach the servos
  servo1.attach(s1pin, s1min, s1MAX);
  servo2.attach(s2pin, s2min, s2MAX);
  servo3.attach(s3pin, s3min, s3MAX);
  servo4.attach(s4pin, s4min, s4MAX);
  servo5.attach(s5pin, s5min, s5MAX);
  servo6.attach(s6pin, s6min, s6MAX);

  //obtain millis time
  moveTime = millis(); //get the millisecond time

  //initialize switch pins
  pinMode(sJ1, INPUT_PULLUP);
  pinMode(sJ2, INPUT_PULLUP);
  pinMode(sJ3, INPUT_PULLUP);
  pinMode(pB, INPUT_PULLUP);

  //read switch pins
  sJ1new = digitalRead(sJ1);
  sJ2new = digitalRead(sJ2);
  sJ3new = digitalRead(sJ3);
  pBnew = digitalRead(pB);

  //home the servo to initial position
  //  homePosition();
  servo1.writeMicroseconds(s1ini); //move servo 1 in the base
  servo2.writeMicroseconds(s2ini); //move servo 2 in link 1
  servo3.writeMicroseconds(s3ini); //move servo 3 in link 1
  servo4.writeMicroseconds(s4ini); //move servo 4 in link 2
  servo5.writeMicroseconds(s5ini); //move servo 5 before tool plate
  servo6.writeMicroseconds(s6ini); //open and close end effector

  //debug
  //  Serial.begin(9600);
}


//----RESET----
void(* resetFunc) (void) = 0;



//***************************************    LOOP    ************************************************
void loop() {
  //read joystick button 1
  sJ1old = sJ1new;
  sJ1new = digitalRead(sJ1);
  if (sJ1old == 1 && sJ1new == 0) {
    spin();
  }

  //read joystick button 2
  sJ2old = sJ2new;
  sJ2new = digitalRead(sJ2);
  if (sJ2old == 1 && sJ2new == 0) {
    grabCan();
  }

  //read joystick button 3
  sJ3old = sJ3new;
  sJ3new = digitalRead(sJ3);
  if (sJ3old == 1 && sJ3new == 0) {
    wave();
  }

  //read pushbutton
  pBold = pBnew;
  pBnew = digitalRead(pB);
  if (pBold == 1 && pBnew == 0) {
    resetFunc();
  }

  //else move the servos normally
  else {
    readJoysticks();
    moveServos();

  }
}
//**********************************************************************************************************


//-------------------------------------FUNCTIONS----------------------------------------------
//----------------------------------------------------reading JOYSTICKS-----------------------------------------------


// %%%%%%%%%%%%%%%%%%%%%%%%%%%%%%%%%%%%%%%%%%%%%%%
void readJoysticks() {
  //---------------------------finding the position of Servo1 motion---------------
  currTime = millis(); //get the current millisecond time
  if (currTime - moveTime >= readtime ) {   //if the difference between move time and current time is the delay period, then
    moveTime = currTime; //update move time
    readJoy1();
    readJoy2();
    readJoy3();
    readJoy4();
    readJoy5();
    readJoy6();
  }
}

// %%%%%%%%%%%%%%%%%%%%%%%%%%%%%%%%%%%%%%%%%%%%
void readJoy1() {
  int v1 = analogRead(J1x); //reads the jostick X-value

  //jostick vals go from 0-to-1023 where 500-550 is a deadband to prevent servo motion when it returns back home
  if (v1 > 800) { //above the positive deadband
    pos1++; //increment the position of servo
  }
  else if (v1 < 200) {  //below the negative deadband
    pos1--; //decrement the position of servo
  }

  pos1cons = constrain(pos1, 0, 1023); //constrained position of joystick x-val
  pos1final = map(pos1cons, 0, 1023, s1min, s1MAX); //map joy-val to servo-microsecond value
  pos1 = pos1cons; //equal pos1 to pos1constrained to prevent going over the constrained range
}

// %%%%%%%%%%%%%%%%%%%%%%%%%%%%%%%%%%%%%%%%%%%%


// %%%%%%%%%%%%%%%%%%%%%%%%%%%%%%%%%%%%%%%%%%%%
void readJoy2() {
  int v2 = analogRead(J1y);
  if (v2 > 800) { //above the positive deadband
    pos2++;
  }
  else if (v2 < 200) {  //below the negative deadband
    pos2--;
  }
  pos2cons = constrain(pos2, 0, 1023);
  pos2final = map(pos2, 0, 1023, s2min, s2MAX);
  pos2 = pos2cons;

}
// %%%%%%%%%%%%%%%%%%%%%%%%%%%%%%%%%%%%%%%%%%%%

// %%%%%%%%%%%%%%%%%%%%%%%%%%%%%%%%%%%%%%%%%%%%
void readJoy3() {
  int v3 = analogRead(J3y);
  if (v3 > 800) { //above the positive deadband
    pos3++;
  }
  else if (v3 < 200) {  //below the negative deadband
    pos3--;
  }

  pos3cons = constrain(pos3, 0, 1023);
  pos3final = map(pos3, 0, 1023, s3min, s3MAX);
  pos3 = pos3cons;
  //  Serial.print("3:  ");
  //  Serial.println(pos3final);
}
// %%%%%%%%%%%%%%%%%%%%%%%%%%%%%%%%%%%%%%%%%%%%


// %%%%%%%%%%%%%%%%%%%%%%%%%%%%%%%%%%%%%%%%%%%%
void readJoy4() {
  int v4 = analogRead(J3x);
  if (v4 > 800) { //above the positive deadband
    pos4++;
  }
  else if (v4 < 200) {  //below the negative deadband
    pos4--;
  }
  pos4cons = constrain(pos4, 0, 1023);
  pos4final = map(pos4, 0, 1023, s4min, s4MAX);
  pos4 = pos4cons;

}
// %%%%%%%%%%%%%%%%%%%%%%%%%%%%%%%%%%%%%%%%%%%%


// %%%%%%%%%%%%%%%%%%%%%%%%%%%%%%%%%%%%%%%%%%%%
void readJoy5() {
  int v5 = analogRead(J2x);
  if (v5 > 800) { //above the positive deadband
    pos5++;
  }
  else if (v5 < 200) {  //below the negative deadband
    pos5--;
  }
  pos5cons = constrain(pos5, 0, 1023);
  pos5final = map(pos5, 0, 1023, s5min, s5MAX);
  pos5 = pos5cons;
}
// %%%%%%%%%%%%%%%%%%%%%%%%%%%%%%%%%%%


// %%%%%%%%%%%%%%%%%%%%%%%%%%%%%%%%%%%
void readJoy6() {
  int v6 = analogRead(J2y);
  if (v6 > 800) { //above the positive deadband
    pos6 = pos6 + gripperspeed;
  }
  else if (v6 < 200) {  //below the negative deadband
    pos6 = pos6 - gripperspeed;
  }
  pos6cons = constrain(pos6, 0, 1023);
  pos6final = map(pos6, 0, 1023, s6min, s6MAX);
  pos6 = pos6cons;
  //  Serial.print("6:  ");
  //  Serial.println(pos6final);

}
// %%%%%%%%%%%%%%%%%%%%%%%%%%%%%%%%%%%

void moveServos() {

  servo1.writeMicroseconds(pos1final); //move servo 1 in the base
  servo2.writeMicroseconds(pos2final); //move servo 2 in link 1
  servo3.writeMicroseconds(pos3final); //move servo 3 in link 1
  servo4.writeMicroseconds(pos4final); //move servo 4 in link 2
  servo5.writeMicroseconds(pos5final); //move servo 5 before tool plate
  servo6.writeMicroseconds(pos6final); //open and close end effector

}

void spin() {


    movePreset(2, 1675, 2000);
    delay(50);
    movePreset(3, 1400, 1725);
    delay(50);
    movePreset(5, 1550, 1900);
    delay(50);
    movePreset(1, 1390, 1400);
    delay(50);

    movePreset(2,2000, 1990);
    movePreset(3, 1800, 1810);
    movePreset(5, 1900, 1910);

    movePreset(2,1990, 1980);
    movePreset(3, 1810, 1820);
    movePreset(5, 1910, 1920);

    movePreset(2,1980, 1970);
    movePreset(3, 1820, 1830);
    movePreset(5, 1920, 1930);

    movePreset(2,1970, 1960);
    movePreset(3, 1830, 1840);
    movePreset(5, 1930, 1940);

    movePreset(2,1960, 1950);
    movePreset(3, 1840, 1850);
    movePreset(5, 1940, 1950);

    movePreset(2,1950, 1940);
    movePreset(3, 1850, 1860);
    movePreset(5, 1950, 1960);

    movePreset(2,1940, 1930);
    movePreset(3, 1860, 1870);
    movePreset(5, 1960, 1970);

    movePreset(2,1930, 1920);
    movePreset(3, 1870, 1880);
    movePreset(5, 1970, 1980);

    movePreset(2,1920, 1910);
    movePreset(3, 1880, 1890);
    movePreset(5, 1980, 1990);

    movePreset(2,1910, 1900);
    movePreset(3, 1890, 1900);
    movePreset(5, 1990, 2000);

    movePreset(2,1900, 1890);
    movePreset(3, 1900, 1910);
    movePreset(5, 2000, 2010);

    movePreset(2,1890, 1880);
    movePreset(3, 1910, 1920);
    movePreset(5, 2010, 2020);

    movePreset(2,1880, 1870);
    movePreset(3, 1920, 1930);
    movePreset(5, 2020, 2030);

    movePreset(2,1870, 1860);
    movePreset(3, 1930, 1940);
    movePreset(5, 2030, 2040);

    movePreset(2,1860, 1850);
    movePreset(3, 1940, 1950);
    movePreset(5, 2040, 2050);

    movePreset(2,1850, 1840);
    movePreset(3, 1950, 1960);
    movePreset(5, 2050, 2060);

    movePreset(2,1840, 1830);
    movePreset(3, 1960, 1970);
    movePreset(5, 2060, 2070);

    movePreset(2,1830, 1820);
    movePreset(3, 1970, 1980);
    movePreset(5, 2070, 2080);

    movePreset(2,1820, 1810);
    movePreset(3, 1980, 1990);
    movePreset(5, 2080, 2090);

    movePreset(2,1810, 1800);
    movePreset(3, 1990, 2000);
    movePreset(5, 2090, 2100);
    delay(500);

    movePreset(1, 1400, 1300);
    delay(500);

    movePreset(2, 1800, 1810);
    movePreset(3, 2000, 1990);
    movePreset(5, 2100, 2090);

    movePreset(2, 1810, 1820);
    movePreset(3, 1990, 1980);
    movePreset(5, 2090, 2080);

    movePreset(2, 1820, 1830);
    movePreset(3, 1980, 1970);
    movePreset(5, 2080, 2070);

    movePreset(2, 1830, 1840);
    movePreset(3, 1970, 1960);
    movePreset(5, 2070, 2060);

    movePreset(2, 1840, 1850);
    movePreset(3, 1960, 1950);
    movePreset(5, 2060, 2050);

    movePreset(2, 1850, 1860);
    movePreset(3, 1950, 1940);
    movePreset(5, 2050, 2040);

    movePreset(2, 1860, 1870);
    movePreset(3, 1940, 1930);
    movePreset(5, 2040, 2030);

    movePreset(2, 1870, 1880);
    movePreset(3, 1930, 1920);
    movePreset(5, 2030, 2020);

    movePreset(2, 1880, 1890);
    movePreset(3, 1920, 1910);
    movePreset(5, 2020, 2010);

    movePreset(2, 1890, 1900);
    movePreset(3, 1910, 1900);
    movePreset(5, 2010, 2000);

    movePreset(2, 1900, 1910);
    movePreset(3, 1900, 1890);
    movePreset(5, 2000, 1990);

    movePreset(2, 1910, 1920);
    movePreset(3, 1890, 1880);
    movePreset(5, 1990, 1980);

    movePreset(2, 1920, 1930);
    movePreset(3, 1880, 1870);
    movePreset(5, 1980, 1970);

    movePreset(2, 1930, 1940);
    movePreset(3, 1870, 1860);
    movePreset(5, 1970, 1960);

    movePreset(2, 1940, 1950);
    movePreset(3, 1860, 1850);
    movePreset(5, 1960, 1950);

    movePreset(2, 1950, 1960);
    movePreset(3, 1850, 1840);
    movePreset(5, 1950, 1940);

    movePreset(2, 1960, 1970);
    movePreset(3, 1840, 1830);
    movePreset(5, 1940, 1930);

    movePreset(2, 1970, 1980);
    movePreset(3, 1830, 1820);
    movePreset(5, 1930, 1920);

    movePreset(2, 1980, 1990);
    movePreset(3, 1820, 1810);
    movePreset(5, 1920, 1910);

    movePreset(2, 1990, 2000);
    movePreset(3, 1810, 1800);
    movePreset(5, 1910, 1900);

    delay(50);


    movePreset(5, 1900, 1600);
    movePreset(3, 1800, 1900); // new letter
    delay(50);
    movePreset(2, 2000, 1675);
    delay(50);
    

    movePreset(1, 1300, 1150); //start next letter

    movePreset(5, 1600, 1900);
    delay(50);
    movePreset(3, 1600, 1725);
    delay(50);
    movePreset(2, 1675, 2000);
    delay(50);
    

    movePreset(1, 1150, 1250);

    delay(50);

    movePreset(2,2000, 1990);
    movePreset(3, 1800, 1810);
    movePreset(5, 1900, 1910);

    movePreset(2,1990, 1980);
    movePreset(3, 1810, 1820);
    movePreset(5, 1910, 1920);

    movePreset(2,1980, 1970);
    movePreset(3, 1820, 1830);
    movePreset(5, 1920, 1930);

    movePreset(2,1970, 1960);
    movePreset(3, 1830, 1840);
    movePreset(5, 1930, 1940);

    movePreset(2,1960, 1950);
    movePreset(3, 1840, 1850);
    movePreset(5, 1940, 1950);

    movePreset(2,1950, 1940);
    movePreset(3, 1850, 1860);
    movePreset(5, 1950, 1960);

    movePreset(2,1940, 1930);
    movePreset(3, 1860, 1870);
    movePreset(5, 1960, 1970);

    movePreset(2,1930, 1920);
    movePreset(3, 1870, 1880);
    movePreset(5, 1970, 1980);

    movePreset(2,1920, 1910);
    movePreset(3, 1880, 1890);
    movePreset(5, 1980, 1990);

    movePreset(2,1910, 1900);
    movePreset(3, 1890, 1900);
    movePreset(5, 1990, 2000);

    movePreset(2,1900, 1890);
    movePreset(3, 1900, 1910);
    movePreset(5, 2000, 2010);

    movePreset(2,1890, 1880);
    movePreset(3, 1910, 1920);
    movePreset(5, 2010, 2020);

    movePreset(2,1880, 1870);
    movePreset(3, 1920, 1930);
    movePreset(5, 2020, 2030);

    movePreset(2,1870, 1860);
    movePreset(3, 1930, 1940);
    movePreset(5, 2030, 2040);

    movePreset(2,1860, 1850);
    movePreset(3, 1940, 1950);
    movePreset(5, 2040, 2050);

    movePreset(2,1850, 1840);
    movePreset(3, 1950, 1960);
    movePreset(5, 2050, 2060);

    movePreset(2,1840, 1830);
    movePreset(3, 1960, 1970);
    movePreset(5, 2060, 2070);

    movePreset(2,1830, 1820);
    movePreset(3, 1970, 1980);
    movePreset(5, 2070, 2080);

    movePreset(2,1820, 1810);
    movePreset(3, 1980, 1990);
    movePreset(5, 2080, 2090);

    movePreset(2,1810, 1800);
    movePreset(3, 1990, 2000);
    movePreset(5, 2090, 2100);
    delay(100);

    movePreset(1, 1250, 1150);
    


    delay(5000);



   //delay(500);
   //movePreset(6, 1495, 1000);
   //movePreset(1, 2087, 500);
   //for (pos = 0; pos <= 180; pos += 1) { // goes from 0 degrees to 180 degrees
    // in steps of 1 degree
   //  servo1.write(pos);              // tell servo to go to position in variable 'pos'
    // delay(50);                       // waits 15ms for the servo to reach the position
   //}
   //for (pos = 180; pos >= 0; pos -= 1) { // goes from 180 degrees to 0 degrees
   //  servo1.write(pos);              // tell servo to go to position in variable 'pos'
   // delay(50);                       // waits 15ms for the servo to reach the position
   //}
   //movePreset(1, 500, 2087);
   //movePreset(6, 1000, 1495);
   //delay(500); 

    resetFunc();
}

void wave() {

  movePreset(2, 1600, 1675);
  movePreset(3, 1380, 1400);
  movePreset(5, 1701, 1418);
  delay(500);
  movePreset(6, 1495, 1000);
  delay(1000);
  int count = 0;
  while (count <= 10) {
    for (pos = 0; pos <= 180; pos += 2) { // goes from 0 degrees to 180 degrees
      // in steps of 1 degree
      servo5.write(pos);              // tell servo to go to position in variable 'pos'
      delay(25);                       // waits 15ms for the servo to reach the position
    }
    for (pos = 180; pos >= 0; pos -= 2) { // goes from 180 degrees to 0 degrees
      servo5.write(pos);              // tell servo to go to position in variable 'pos'
      delay(25);                       // waits 15ms for the servo to reach the position

    }
    delay(10);
    count = count + 1;
  }
  delay(1000);
   //movePreset(6, 1000, 1495);
   //movePreset(2, 1150, 1300);
   //movePreset(3, 1800, 2050);
  resetFunc();
}



void grabCan() {

  movePreset(1, 1425, 1400);
  delay(1000);

  movePreset(2, 1700, 1675);
  delay(1000); 

  movePreset(3, 1425, 1400);
  delay(1000);

  movePreset(4, 1525, 1500);
  delay(1000);

  movePreset(5, 1575, 1550);
  delay(1000);

  movePreset(6, 1400, 1375);
  delay(2000);
  // for Q = 1:1000
  
  delay(1000000000000);
 // movePreset(5, 1700, 1200);
  //movePreset(2, 1300, 1500); //2
 // movePreset(3, 2050, 2500); //3

  //  movePreset(5, 1200, 1450); //5
 // movePreset(6, 1500, 1000); //6
 // movePreset(2, 1515, 1300);
 // movePreset(3, 2500, 1700); //2
  //movePreset(5, 1200, 1685); //1
  //delay(1);
 // movePreset(1, 2088, 1450); //3
  //delay(1);
  //movePreset(2, 1300, 1515);

 // movePreset(4, 1500, 2318); //5

  //delay(2);

  //reverse
  //movePreset(4, 2318, 1500);
 // movePreset(5, 1685, 1481);
 // movePreset(2, 1515, 1300);
  //delay(1);
 // movePreset(1, 1450, 2088);
  //delay(1);

 // movePreset(3, 1700, 2150);
 // movePreset(2, 1300, 1450);
 // movePreset(6, 1100, 1500);




 // movePreset(3, 2150, 2050);
  //movePreset(2, 1450, 1300);
  //movePreset(5, 1481, 1700);
  //delay(2);
  // resetFunc();
}


void movePreset(int servoNum, int startPos, int endPos) {
  int dtime = 5;
  if (endPos > startPos) {
    if (servoNum == 1) {
      for (pos1 = startPos; pos1 <= endPos; pos1++) {
        servo1.writeMicroseconds(pos1);
        delay(dtime);
      }
    }
    if (servoNum == 2) {
      for (pos2 = startPos; pos2 <= endPos; pos2++) {
        servo2.writeMicroseconds(pos2);
        delay(dtime);
      }
    }
    if (servoNum == 3) {
      for (pos3 = startPos; pos3 <= endPos; pos3++) {
        servo3.writeMicroseconds(pos3);
        delay(dtime);
      }
    }
    if (servoNum == 4) {
      for (pos4 = startPos; pos4 <= endPos; pos4++) {
        servo4.writeMicroseconds(pos4);
        delay(dtime);
      }
    }
    if (servoNum == 5) {
      for (pos5 = startPos; pos5 <= endPos; pos5++) {
        servo5.writeMicroseconds(pos5);
        delay(dtime);
      }
    }
    if (servoNum == 6) {
      for (pos6 = startPos; pos6 <= endPos; pos6++) {
        servo6.writeMicroseconds(pos6);
        delay(dtime);
      }
    }
  }
  else if (endPos < startPos) {
    if (servoNum == 1) {
      for (pos1 = startPos; pos1 >= endPos; pos1--) {
        servo1.writeMicroseconds(pos1);
        delay(dtime);
      }
    }
    if (servoNum == 2) {
      for (pos2 = startPos; pos2 >= endPos; pos2--) {
        servo2.writeMicroseconds(pos2);
        delay(dtime);
      }
    }
    if (servoNum == 3) {
      for (pos3 = startPos; pos3 >= endPos; pos3--) {
        servo3.writeMicroseconds(pos3);
        delay(dtime);
      }
    }
    if (servoNum == 4) {
      for (pos4 = startPos; pos4 >= endPos; pos4--) {
        servo4.writeMicroseconds(pos4);
        delay(dtime);
      }
    }
    if (servoNum == 5) {
      for (pos5 = startPos; pos5 >= endPos; pos5--) {
        servo5.writeMicroseconds(pos5);
        delay(dtime);
      }
    }
    if (servoNum == 6) {
      for (pos6 = startPos; pos6 >= endPos; pos6--) {
        servo6.writeMicroseconds(pos6);
        delay(dtime);
      }
    }

  }
}
